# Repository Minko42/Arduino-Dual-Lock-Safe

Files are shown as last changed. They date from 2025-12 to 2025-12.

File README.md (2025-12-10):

# Arduino Dual-Lock Safe

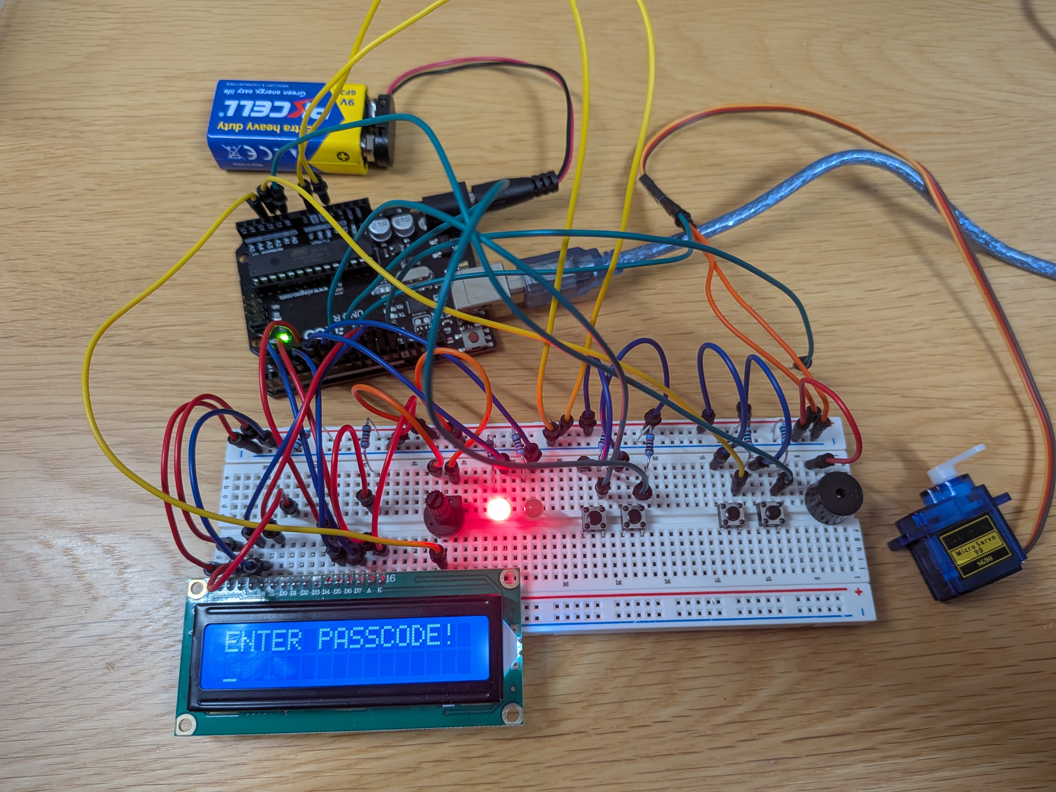
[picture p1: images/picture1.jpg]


## 1. Abstract (概要)
* **What:** Arduino Unoを用いたデジタル・アナログパスコードで動く金庫システム。
* **Why:** C++ベースのArduino言語を用いて、組み込みシステムの理解を深めるため。
* **Result:** 「ボタン入力（デジタル）」に加え、「ダイヤル操作（アナログ）」を組み合わせた2段階認証（2-Factor Authentication）が可能。

## 2. Motivation (背景と目的)
* 学部のArduinoを使った授業で作品を作る機会があった。
* 授業で学習したことと、自分で調べて身に着けた知識を形にするため。

## 3. Technical Specifications (技術仕様)

### Hardware
| Component | Model | Notes |
| --- | --- | --- |
| MCU | Arduino Uno R3 | ATmega328P,5V |
| Potentiometer | PT-15 |  |
| 5mm LED (Red) | RL5-R5015 | Super-Red (631nm) |
| 5mm LED (Green) | RL5-G8020 | Super-Green (525nm) |
| LCD Module | LCM1602A | 16x2 character LCD module |
| Passive Buzzer |  | 5V Passive buzzer |
| Micro Servo Motor | SG90 | 4.8-6V |
| 9V Lithium Battery | U9VL-J-P | 1200mAh |

### Software
* **Language:** C++ / Arduino Language
* **IDE:** Arduino IDE 2.3.6
* **Key Libraries:** 
  * stdlib.h
  * Servo.h
  * LiquidCrystal.h

## 4. Design & Theory (設計と原理)

### 4.1 Circuit Design (回路設計)
回路図は `hardware` フォルダ内のPDFを参照してください。
* [Circuit Diagram (PDF)](hardware/schematics.pdf)

**Component Selection (部品選定の根拠):**
* **LED電流制限抵抗:**
  LEDの順電圧 $V_f = 2.0V$(赤色)、$3.6V$(緑色)、目標電流 $I_f = 20mA$ と仮定( [LED_datasheet(PDF)](docs/LED_datasheet.pdf) より)。Arduinoの出力は $5V$ なので、オームの法則より
  $$R = \frac{5.0 - V_f}{I_f} $$
  したがって、赤色では $R = 150[\Omega]$ 、緑色では $R = 70[\Omega]$ となり、赤色LEDでは**220Ω**、緑色LEDでは**100Ω**の抵抗を選定した。(後に緑色LEDの抵抗を**220Ω**に変更)

### 4.2 Algorithm (アルゴリズム)
* ボタンを押した瞬間だけでなく、「指を離すまで次の処理に進まない」 というループ処理（while）を組み込むことで、連打ミス（チャタリング）を防いでいる。
* ポテンショメータの細かい数値（0〜1023）をそのまま使わず、map() 関数で 0〜100 の範囲に正規化した。これにより、人間がダイヤルを合わせやすい操作感を実現している。
* 「デジタル入力」→「アナログ入力」→「判定」という手順を、フラグ変数（reset, potenlock）を使って管理している。順序を守らないとロックが開かない仕組みを、シンプルな条件分岐で構築した。

## 5. Experimental Results (実験結果と考察)

### Results
* **パスコードが正しい場合** 
  1. **初期状態:** LCDに `ENTER PASSCODE!` と表示され、赤色LEDが点灯、サーボモータは0度（施錠位置）で固定されている。
  2. **デジタル入力:** タクトスイッチを用いて`1 1 1 1`と入力。LCDの2行目に 1111 と表示された。
  3. **アナログ入力:** ポテンショメータを回し、LCD右側の数値を変化させた。値が 50 になる位置で調整し、Enterキー（A1）を押した。LCDに `L`（Lock）が表示された。
  4. **判定:** Enterキー操作後、直ちに緑色LEDが点灯し、LCDに `CORRECT` と表示された。同時に高い音（1000Hz）が鳴り、サーボモータが90度（解錠位置）へ回転した。

* **パスコードが正しくない場合**
  * デジタルコードのみ誤り
    * **入力:** デジタル 1212 / アナログ 50
    * **結果:** LCDに `WRONG` と表示され、低い音（200Hz）が鳴り、サーボモータは動かなかった（施錠のまま）。
  * アナログコードのみ誤り
    * **入力:** デジタル 1111 / アナログ 80
    * **結果:** デジタルコードのみ誤りの場合と同様に、`WRONG` 表示と共に解錠されなかった。

* **操作性の確認**
  * **ボタン操作:** ボタンを長押ししても連続で数値が入力されることはなく、指を離したタイミングで次の桁へ進む仕様が正常に機能し、誤入力を防げることが確認できた。
  
  * **リセット機能:** 途中どのような段階であっても、リセットボタン（A0）を押すことで初期画面に戻り、変数がリセットされることを確認した。

### Discussion (考察)
実験結果に基づき、本システムのアルゴリズムとハードウェア制御について以下の考察を得た。

**1. セキュリティ強度について（二要素認証の有効性）**
  
  本システムは、離散的な数値（デジタルコード）と連続的な数値（アナログコード）を組み合わせている。単純な4桁のボタン入力（1と2のみ）だけでは $2^4 = 16$ 通りと組み合わせが少ないが、ここにアナログ入力（0〜100）の組み合わせを加えることで、総当たり攻撃に対する耐性が向上している。これは、実際のセキュリティシステムでも用いられる「知識認証（番号）」と「所持認証（鍵の位置など）」に近い多層的なセキュリティ構造を模倣できていると言える。また、ソースコードの変数の値を書き換えるだけで、デジタルコードの長さを最大で10桁に変更することが可能であり、これにより $103424$ 通りまで増やすことが可能である。

**2. 人間工学に基づいた入力処理の工夫**
  
  ソースコード内の `map(analogvalue, 0, 1023, 0, 100)` の処理は、操作性に大きく寄与している。 ポテンショメータの生データ（0〜1023）をそのままパスコードとして使用した場合、人間が手作業で「50」などの特定の値に1単位の狂いもなく合わせることは非常に困難である。これを100段階に縮約（正規化）することで、セキュリティを維持しつつ、人間がストレスなく操作できる許容範囲を設けている点は、ユーザーインターフェース設計として適切であった。

**3. チャタリング対策と確実な入力**
  
  デジタル入力関数において `while(digitalRead... == HIGH)` で「ボタンが離されるのを待つ」処理を入れたことは、誤動作防止に極めて有効であった。Arduinoのループ処理は高速であるため、この待機処理がないと一瞬の押下で複数回分の入力として判定される（チャタリングのような挙動）恐れがある。本システムではこのアルゴリズムにより、意図した通りの桁数を正確に入力できた。

**4. 課題と改善案：アナログ値の判定精度**
  
  操作中、ポテンショメータを 50 に合わせたつもりでも、電気的なノイズや接触抵抗の微細な変化により、内部的に値がふらつく現象が想定される。 現在のコードでは `if(a == b)` と完全一致を求めているため、例えば内部値が 49 と 50 を行き来している瞬間に決定ボタンを押すと、表示は 50 でも判定時にズレて不正解となる可能性がある。 実用性をさらに高めるためには、判定ロジックに「±1〜2程度の誤差を許容する」処理を追加することで、より使いやすいシステムになると考えられる。

## 6. Usage (使い方)
**事前準備**
1. `src/Electric_safe/` 内のコードをArduinoに書き込む。
2. `hardware/schematics.pdf` を参考に配線する。

**1.各部の名称と役割**
* ボタン1（Pin 8）：数字「1」を入力する。
* ボタン2（Pin 9）：数字「2」を入力する。
* ダイヤル（Pin A2）：ポテンショメータを回して「アナログコード」を合わせる。
* 決定キー（Pin A1）：Enterボタン。数値の決定や最終的な解錠に使う。
* リセットキー（Pin A0）：入力を中断し、最初からやり直す時に使う。
* LCD画面：現在の状態や入力した数値が表示される。
* LEDランプ：赤は「ロック中」、緑は「解錠成功」を示す。
* シリアルモニタ：シリアルモニタ上で金庫の状態と入力されたパスコードを確認することができる。

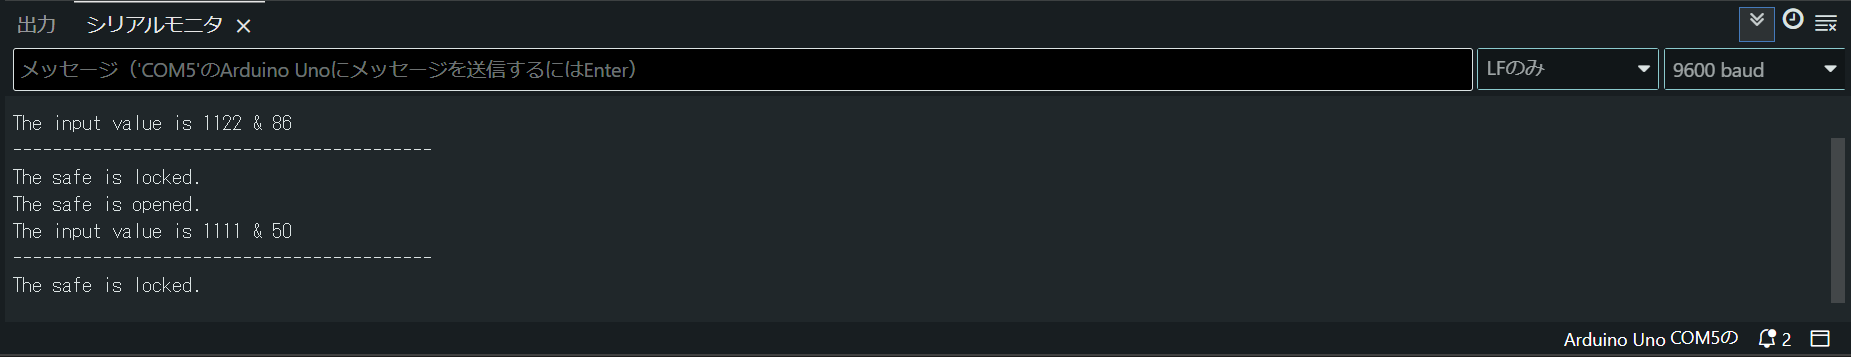
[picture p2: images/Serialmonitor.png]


**2.解錠の手順**
* **手順1:** 起動と確認 
システムを起動すると、LCD画面に ENTER PASSCODE! と表示され、赤色LED が点灯する。（ロック状態）

* **手順2:** ボタン1 と ボタン2 を使って、決められた桁数のパスワードを入力する。（初期設定パスワード:`1 1 1 1`）
ボタンを押すと画面下段に数字が表示され、入力し終わると自動的に次のステップ（ダイヤル入力）へ進む。

* **手順3:** デジタル入力が終わると、カーソルが右側に移動する。 ダイヤルを左右に回して、画面の数字を指定の値に合わせる。（初期設定値: `50`）※ 0〜100の間で数値が変化する。

* **手順4:** ダイヤルの数値を合わせたら、決定キー（Enter） を 1回 押す。画面に L という文字が表示されたら、数値が固定されていることを表す。

* **手順5:** 数値が固定された状態（Lが表示された状態）で、もう一度、決定キー（Enter） を押す。成功であれば画面に CORRECT と表示され、緑色LED が点灯、高い音が鳴り、金庫（サーボモータ）が開く。失敗の場合は画面に WRONG と表示され、低いエラー音が鳴り、ロックは解除されない。

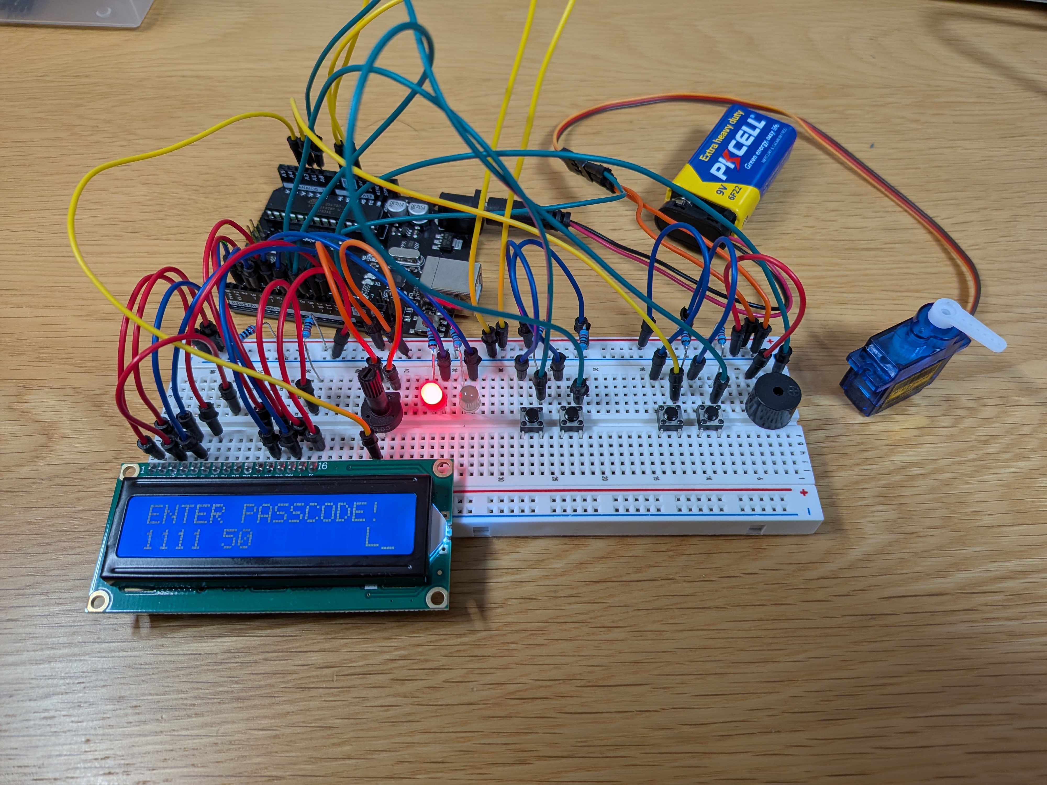
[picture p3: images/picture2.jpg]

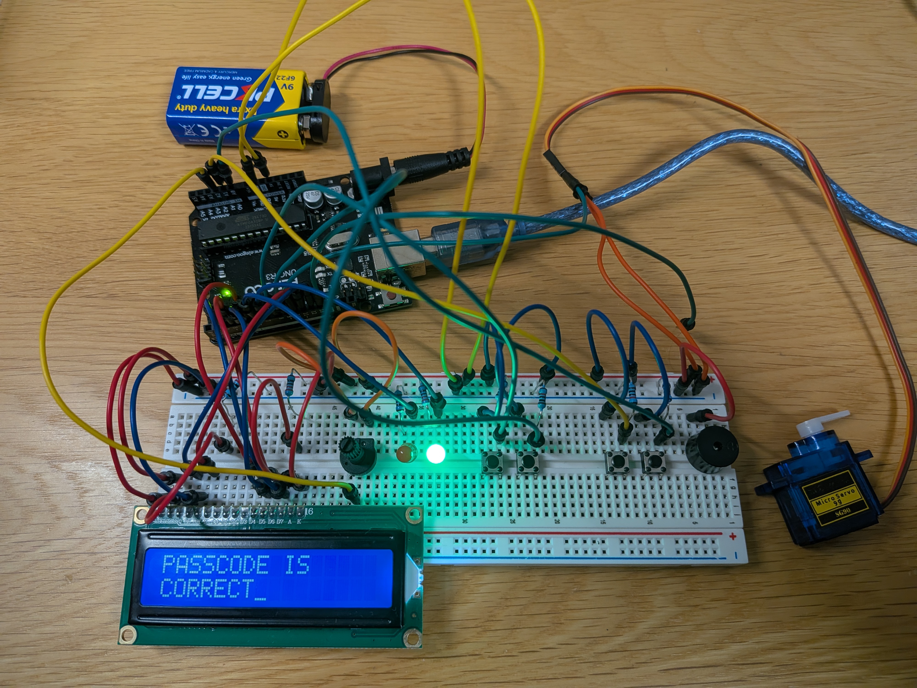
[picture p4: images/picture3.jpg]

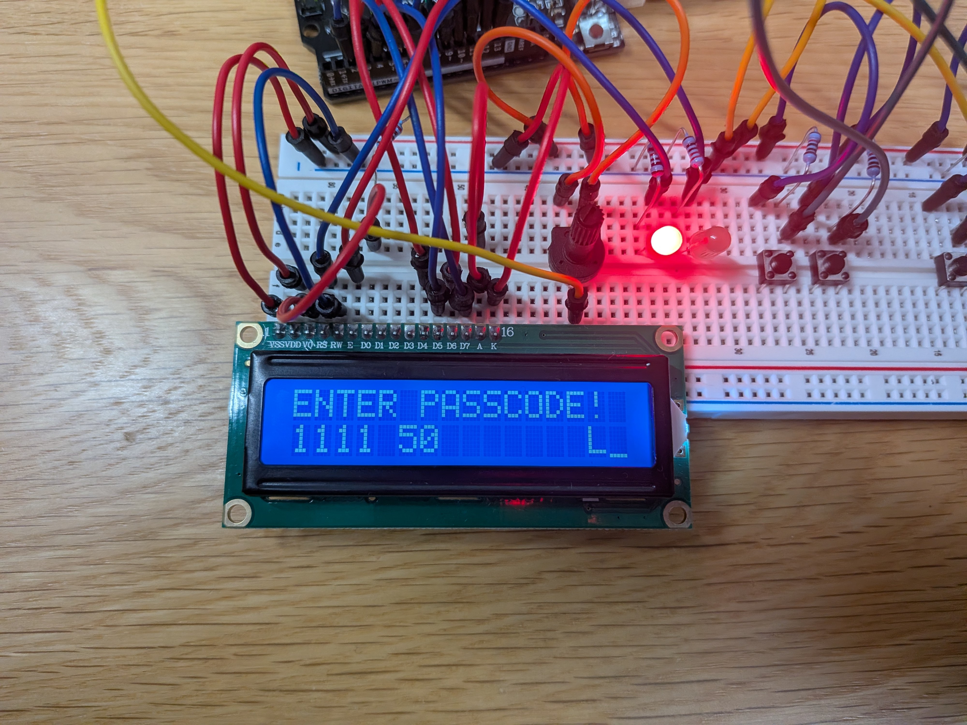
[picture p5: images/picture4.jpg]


**3.施錠（リセット）の方法**

金庫を閉じてロック状態に戻すには、リセットキー を押す。サーボモータが元の位置（0度）に戻り、赤色LED が点灯し、手順1の画面に戻る。

※ 入力を間違えてやり直したい場合も、このボタンを押す。

**4.パスワードの変更方法**

コード内の以下の部分を変更して、Arduinoに書き込むことでパスワードとその桁数をを変更できる。

`#define passlen 4 //１～１０桁まで.`

`const long digitalcode = 1111; //デジタルパスコード.`

`const int analogcode = 50; //アナログパスコード（０～１００まで）.`

*※passlenの"4"の部分はデジタルパスコードの桁数を設定している。*

## 7. References (参考文献)
使用した各部品のデータシートは`docs`フォルダ内のPDFを参照してください。
* 【Arduino入門編⑰】LCDディスプレイに文字を表示させてみる！［前編］[1602 LCDモジュール] (https://burariweb.info/electronic-work/arduino-learning/arduino-lcd-module-display.html)

* kicadの使い方（回路図編）(https://www.kicad.xyz/circuit/)

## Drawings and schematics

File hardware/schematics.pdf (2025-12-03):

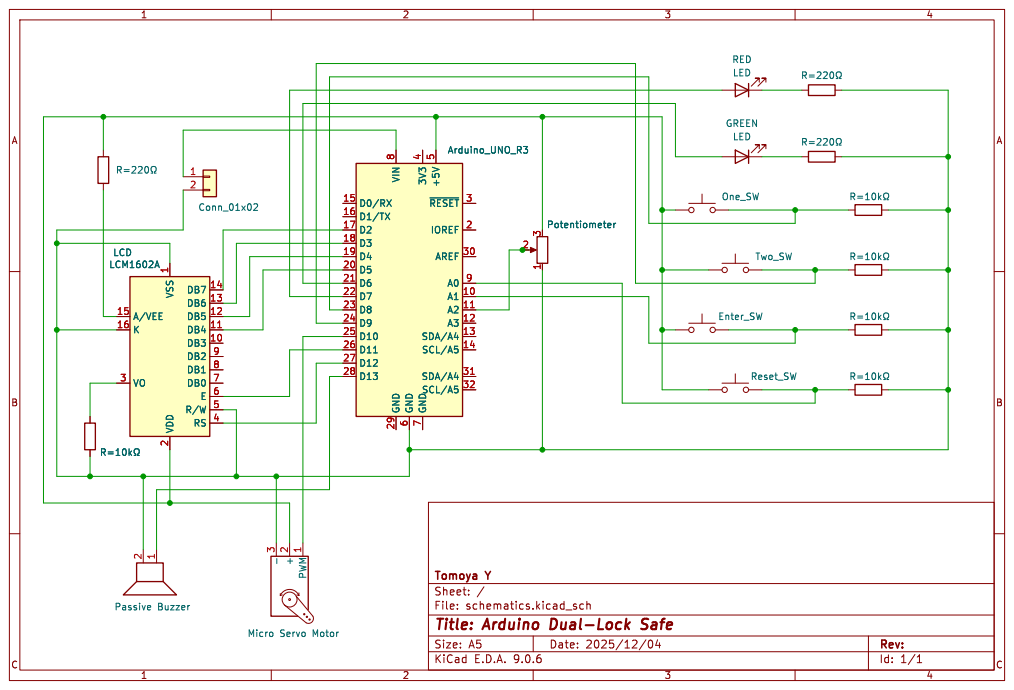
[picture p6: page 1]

RED

File: schematics.kicad_sch Sheet: / Tomoya Y

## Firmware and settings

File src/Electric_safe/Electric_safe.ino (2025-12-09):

#include <stdlib.h>
#include <Servo.h>
Servo myservo;

#include <LiquidCrystal.h>
// [構文]LiquidCrystal(rs, rw,  enable, d0, d1, d2, d3, d4, d5, d6, d7)
LiquidCrystal lcd(12, 11, 5, 4, 3, 2);

//ピン番号の設定
const int R_LEDPin = 6;
const int G_LEDPin = 7;
const int One_Pin = 8;
const int Two_Pin = 9;
const int Servo_Pin = 10;
const int Sound_Pin = 13;
const int Reset_Pin = A0;
const int Enter_Pin = A1;
const int PotenPin = A2;

//定数の設定.
#define openfre 1000
#define opentime 500
#define closefre 200
#define closetime 800
#define passlen 4 //１～１０桁まで.
#define waittime 200

//初期値の設定.
const long digitalcode = 1111; //デジタルパスコード.
const int analogcode = 50; //アナログパスコード（０～１００まで）.

long dcode = 0;
int acode = 0;

bool reset = true;
bool potenlock = true;

//LCDの待機画面を設定する関数.
void lcdstart(){
  lcd.begin(16, 2);
  lcd.clear();
  lcd.setCursor(0, 0);
  lcd.print("ENTER PASSCODE!");
  lcd.cursor();
}

//金庫を開ける関数.
void opensafe(){
  Serial.println("The safe is opened.");
  myservo.write(90);
  digitalWrite(G_LEDPin,HIGH);
  digitalWrite(R_LEDPin,LOW);
}

//金庫を閉じる関数.
void locksafe(){
  Serial.println("The safe is locked.");
  myservo.write(0);
  digitalWrite(G_LEDPin,LOW);
  digitalWrite(R_LEDPin,HIGH);
}

//デジタルパスコードを入力する関数.
long InputDigitalcode() {
  long pass = 0;
  for (int i = 0; i < passlen; i++) {
    lcd.setCursor(i, 1);

    //未入力は-1とする.
    int input_digit = -1;

    while (true) {
      if (digitalRead(One_Pin) == HIGH) {
        input_digit = 1;
      } 
      else if (digitalRead(Two_Pin) == HIGH) {
        input_digit = 2;
      }

      if (input_digit != -1) {
        while (digitalRead(One_Pin) == HIGH || digitalRead(Two_Pin) == HIGH) {
          delay(waittime);
        }
        lcd.print(input_digit);
        pass = (pass * 10) + input_digit;
        break;
      }
    }
  }
  return pass;
}

//アナログパスコードを入力する関数.
int InputAnalogcode(){
  int pass = 0;
  lcd.setCursor(passlen + 1, 1);
  while(true){
    int analogvalue = analogRead(PotenPin);
    pass = map(analogvalue,0,1023,0,100);
    lcd.setCursor(passlen + 1, 1);
    lcd.print(pass);
    lcd.print(" ");

    if(digitalRead(Enter_Pin) == HIGH){
      lcd.setCursor(14,1);
      lcd.print("L");
      potenlock = true;
      delay(waittime);
      break;
    }

     delay(100);
  }
  return pass;
}

//整数の桁数を返す関数.
int digitnum(long a){
  int digit = 0;
  while(a != 0){
    a = a / 10;
    digit++;
  }
  return digit;
}

//入力されたパスコードが正しいか判定する関数.
bool check(long a, long b){
  if(a == b){
    return true;
  }
  else{
    return false;
  }
}

//パスコードが異なる場合の処理をする関数.
void wrongpass(){
  lcd.clear();
  lcd.setCursor(0, 0);
  lcd.print("PASSCODE IS");
  lcd.setCursor(0, 1);
  lcd.print("WRONG");
  tone(Sound_Pin,closefre,closetime);
}

//パスコードが正しい場合の処理をする関数.
void correctpass(){
  lcd.clear();
  lcd.setCursor(0, 0);
  lcd.print("PASSCODE IS");
  lcd.setCursor(0, 1);
  lcd.print("CORRECT");
  tone(Sound_Pin,openfre,opentime);
}

//シリアルモニタに入力された値を表示する関数.
void printvalue(long digitalcode, int analogcode){
  Serial.print("The input value is ");
  Serial.print(digitalcode);
  Serial.print(" & ");
  Serial.print(analogcode);
  Serial.println("");
}


void setup() {
  myservo.attach(Servo_Pin,500,2400);
  Serial.begin(9600);

  pinMode(R_LEDPin, OUTPUT);
  pinMode(G_LEDPin, OUTPUT);
  pinMode(Sound_Pin, OUTPUT);
  pinMode(One_Pin, INPUT);
  pinMode(Two_Pin, INPUT);
  pinMode(Reset_Pin, INPUT);
  pinMode(Enter_Pin, INPUT);
}

void loop() {
  while(reset){
    Serial.println("------------------------------------------");
    locksafe();
    lcdstart();
    dcode = InputDigitalcode();
    
    if(digitnum(dcode) == passlen){
      reset = false;
      potenlock = false;
      break;
    }
  }

  while(!potenlock){
    acode = InputAnalogcode(); 
  }

  //エンターキーが押された時の処理.
  if(digitalRead(Enter_Pin) == HIGH){
    if(check(digitalcode,dcode) == true && check(analogcode, acode) == true){
      correctpass();
      opensafe();
    }
    else{
      wrongpass();
    }
    printvalue(dcode,acode);
    delay(waittime);
  }

  //リセットキーが押された時の処理.
  if(digitalRead(Reset_Pin) == HIGH){
    reset = true;
    delay(waittime);
  }
}

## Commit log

2025-12-03 Fix schematics.pdf
    [schematics.kicad_sch]
2025-12-09 fix: change function names
    [Electric_safe.ino]
2025-12-09 fix: modify src and README
    [Electric_safe.ino]
